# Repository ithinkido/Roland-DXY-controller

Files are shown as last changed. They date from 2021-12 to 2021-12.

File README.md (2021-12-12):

# Roland-DXY-controller
 A modern ESP32 based controller for Roland DXY plotter with i2c shift regisers for button mapping, OLED dispay, solenoid drivers and on board TMC 2208 silent stepper drivers. This Design uses standard STEP/DIR controll only.
 This is a two board design with a main controller and a daughter board that handles the USB-C serial connection and SD card. This allows for perfect placement of the connectors and the use of the exsisting openins in the plotter case. 

The board is designed to be a a plug in replacemnt with NO modifications to the existing plotter hardware. 
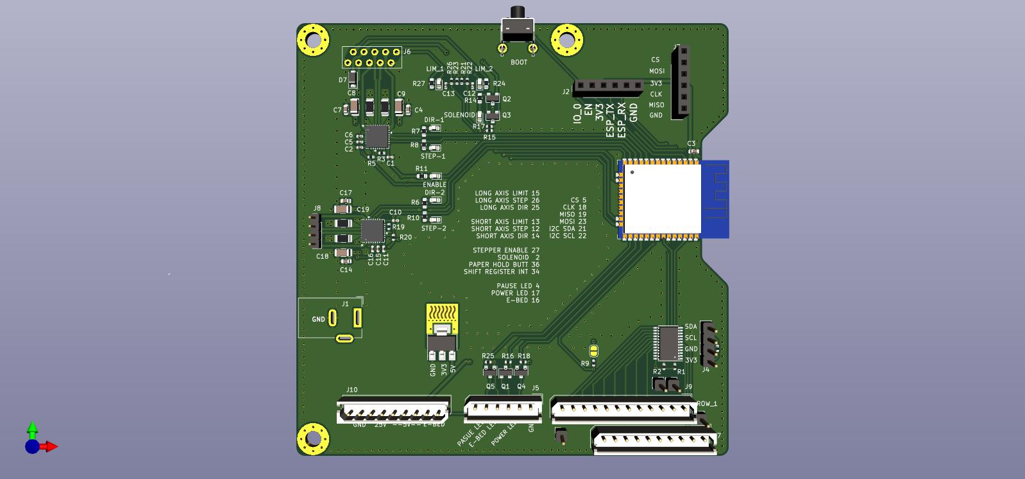
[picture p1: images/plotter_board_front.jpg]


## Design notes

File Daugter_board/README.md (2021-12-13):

This board takes care of the USB-C serial comms as well as the SD card. It is piggybacked onto the main board to postion the connectors correctly within the case openings.  

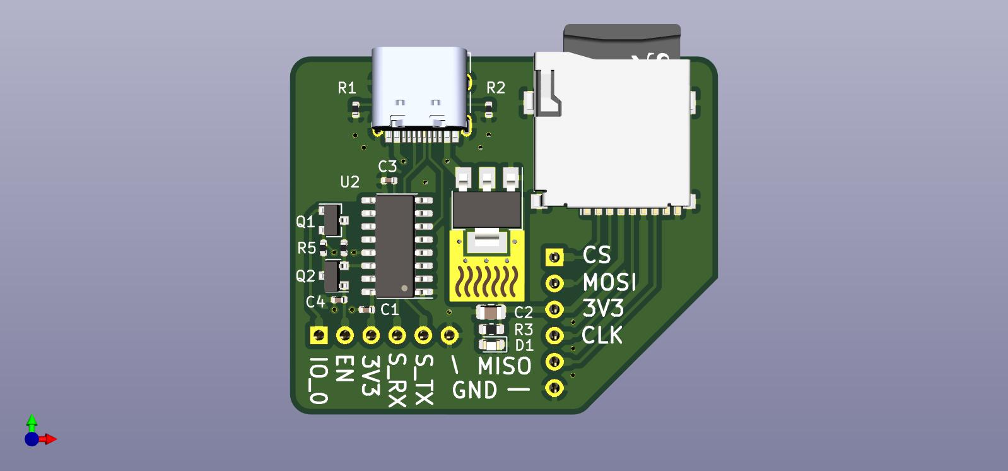
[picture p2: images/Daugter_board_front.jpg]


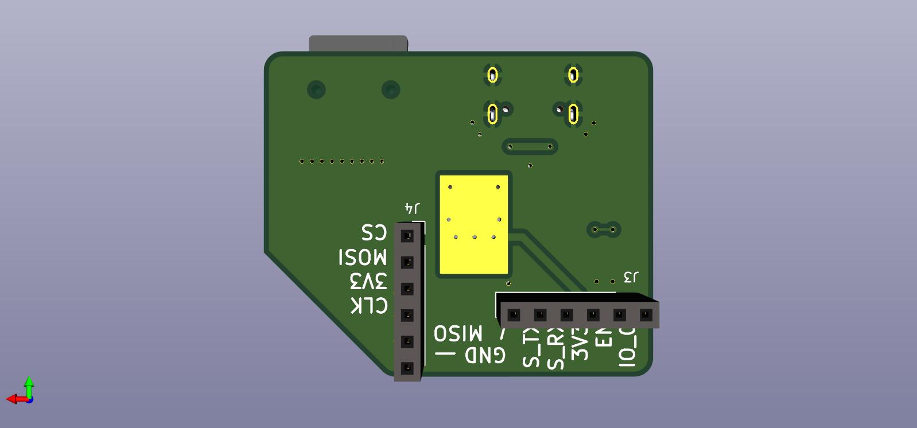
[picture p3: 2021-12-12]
images/Daugter_board_back.jpg

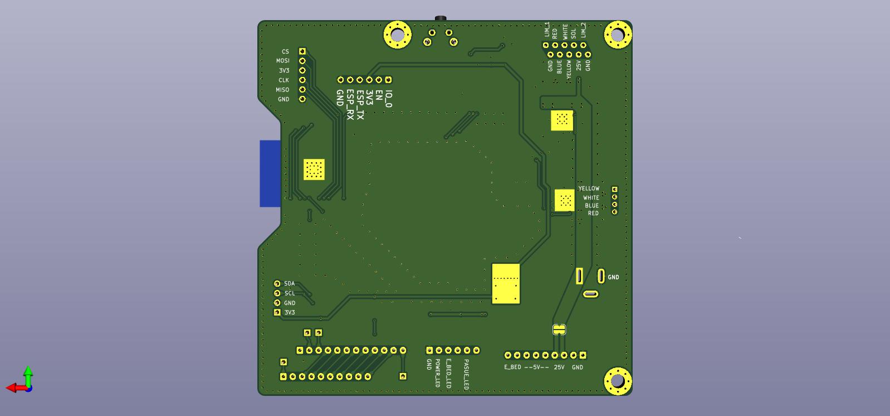
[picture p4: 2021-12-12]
images/plotter_board_back.jpg

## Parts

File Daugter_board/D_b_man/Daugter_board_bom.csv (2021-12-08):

Comment | Designator | Footprint | LCSC
10K | R5,R4 | Resistor_SMD:R_0402_1005Metric | C25744
MMBT3904 | Q1,Q2 | Package_TO_SOT_SMD:SOT-23 | C20526
USB_C_Receptacle_USB2.0 | J1 | Connector_USB:USB_C_Receptacle_HRO_TYPE-C-31-M-12 | C165948
5.1K | R2,R1 | Resistor_SMD:R_0402_1005Metric | C25905
100nf | C4 | Capacitor_SMD:C_0402_1005Metric | C1525
1uF | C1 | Capacitor_SMD:C_0402_1005Metric | C52923
Micro_SD_Card | J2 | plotter_board:Conn_uSDcard | C111196
1uF | C2 | Capacitor_SMD:C_0805_2012Metric | C28323
AP1117-33 | U1 | Package_TO_SOT_SMD:SOT-223-3_TabPin2 | C6186
USB_Serial | J3 | Connector_PinSocket_2.54mm:PinSocket_1x06_P2.54mm_Vertical
SD_Card | J4 | Connector_PinSocket_2.54mm:PinSocket_1x06_P2.54mm_Vertical
100nF | C3 | Capacitor_SMD:C_0402_1005Metric | C1525
2K2 | R3 | Resistor_SMD:R_0603_1608Metric | C4190
CH340B | U2 | Package_SO:SOIC-16_3.9x9.9mm_P1.27mm | C81010
LED | D1 | LED_SMD:LED_0603_1608Metric | C72041

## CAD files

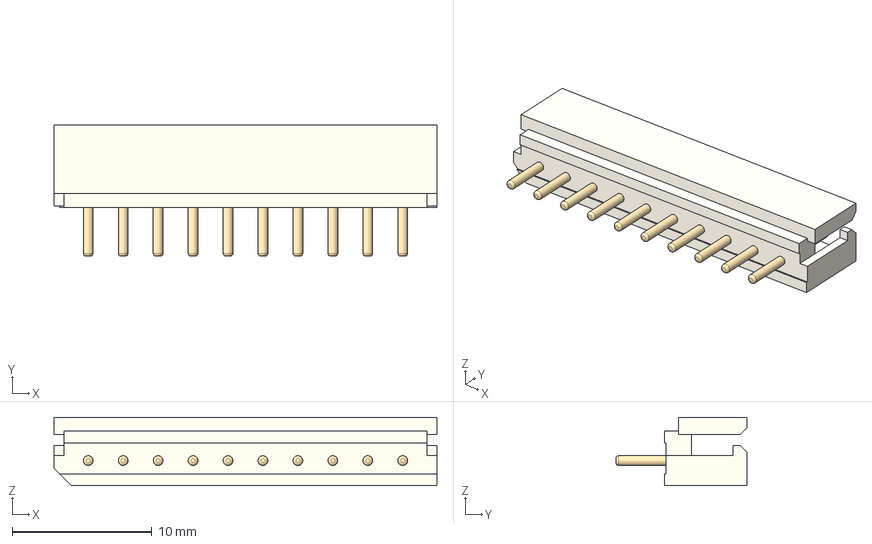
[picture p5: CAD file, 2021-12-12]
3D/Mini_Spox_10pin v2.step
27.4 x 9.40 x 4.90 mm

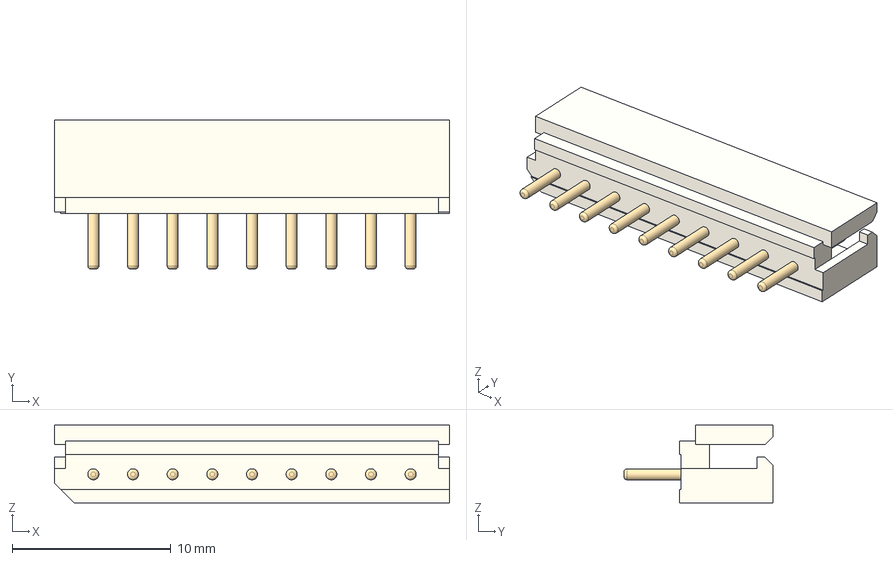
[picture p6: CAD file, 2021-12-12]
3D/Mini_Spox_9pin v2.step
24.9 x 9.40 x 4.90 mm

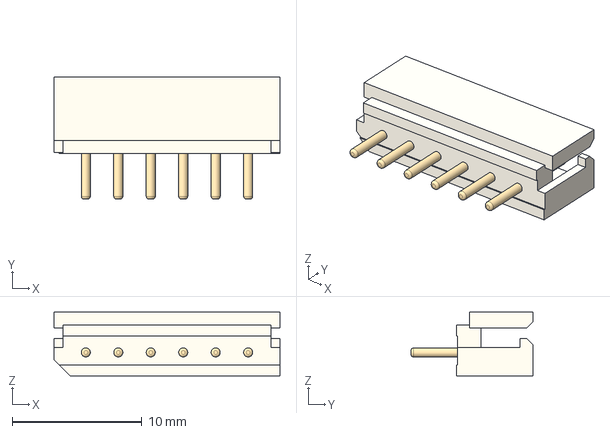
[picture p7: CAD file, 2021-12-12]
3D/Mini_Spox_6pin v3.step
17.4 x 9.40 x 4.90 mm

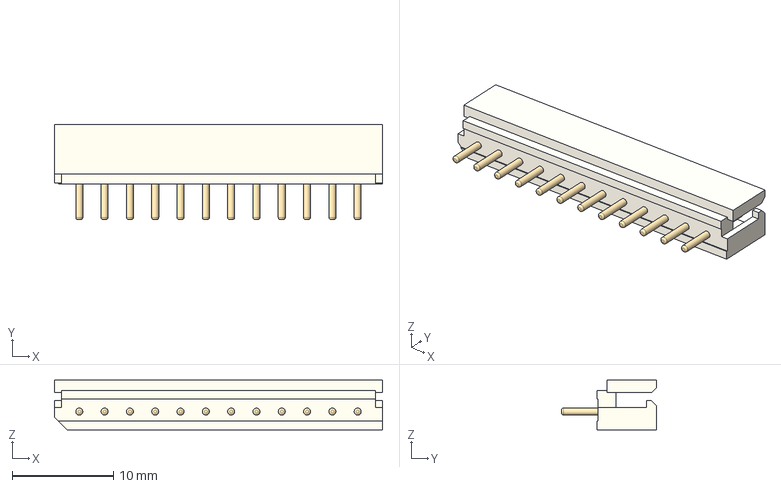
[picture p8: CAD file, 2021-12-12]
3D/Mini_Spox_12pin v2.step
32.4 x 9.40 x 4.90 mm

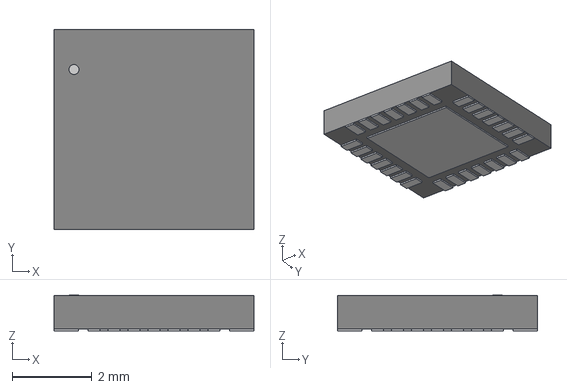
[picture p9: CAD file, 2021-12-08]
3D/QFN28_5X5_TRI.step
5.00 x 5.00 x 0.892 mm

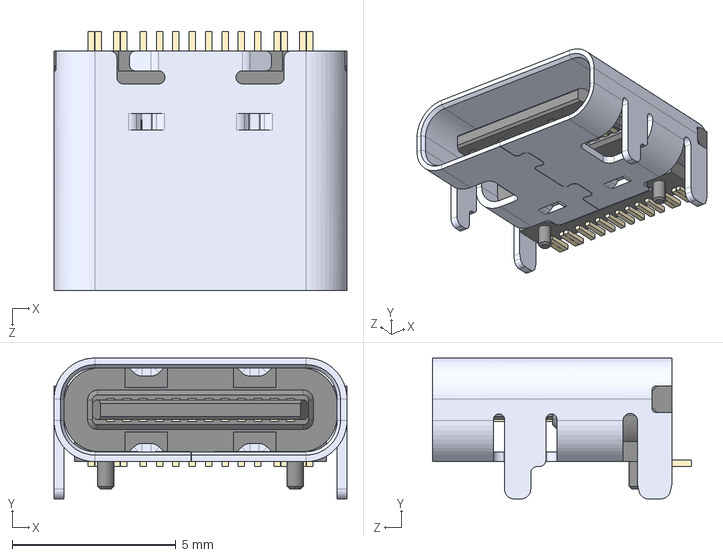
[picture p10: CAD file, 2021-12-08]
3D/TYPE-C-31-M-12--3DModel-STEP-56544.step
8.94 x 4.30 x 7.90 mm

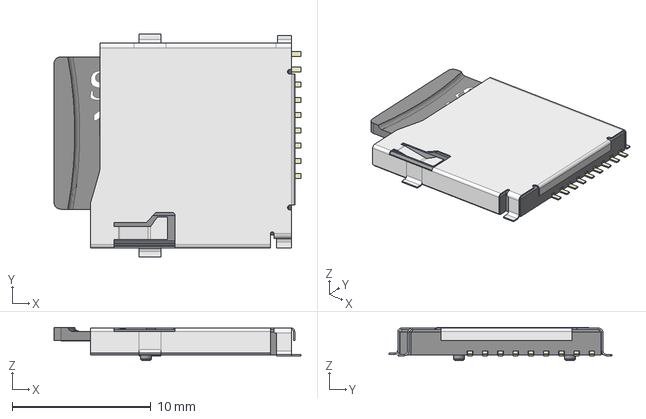
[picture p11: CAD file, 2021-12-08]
3D/TF-15x15_SD_Card.step
17.8 x 16.1 x 2.40 mm

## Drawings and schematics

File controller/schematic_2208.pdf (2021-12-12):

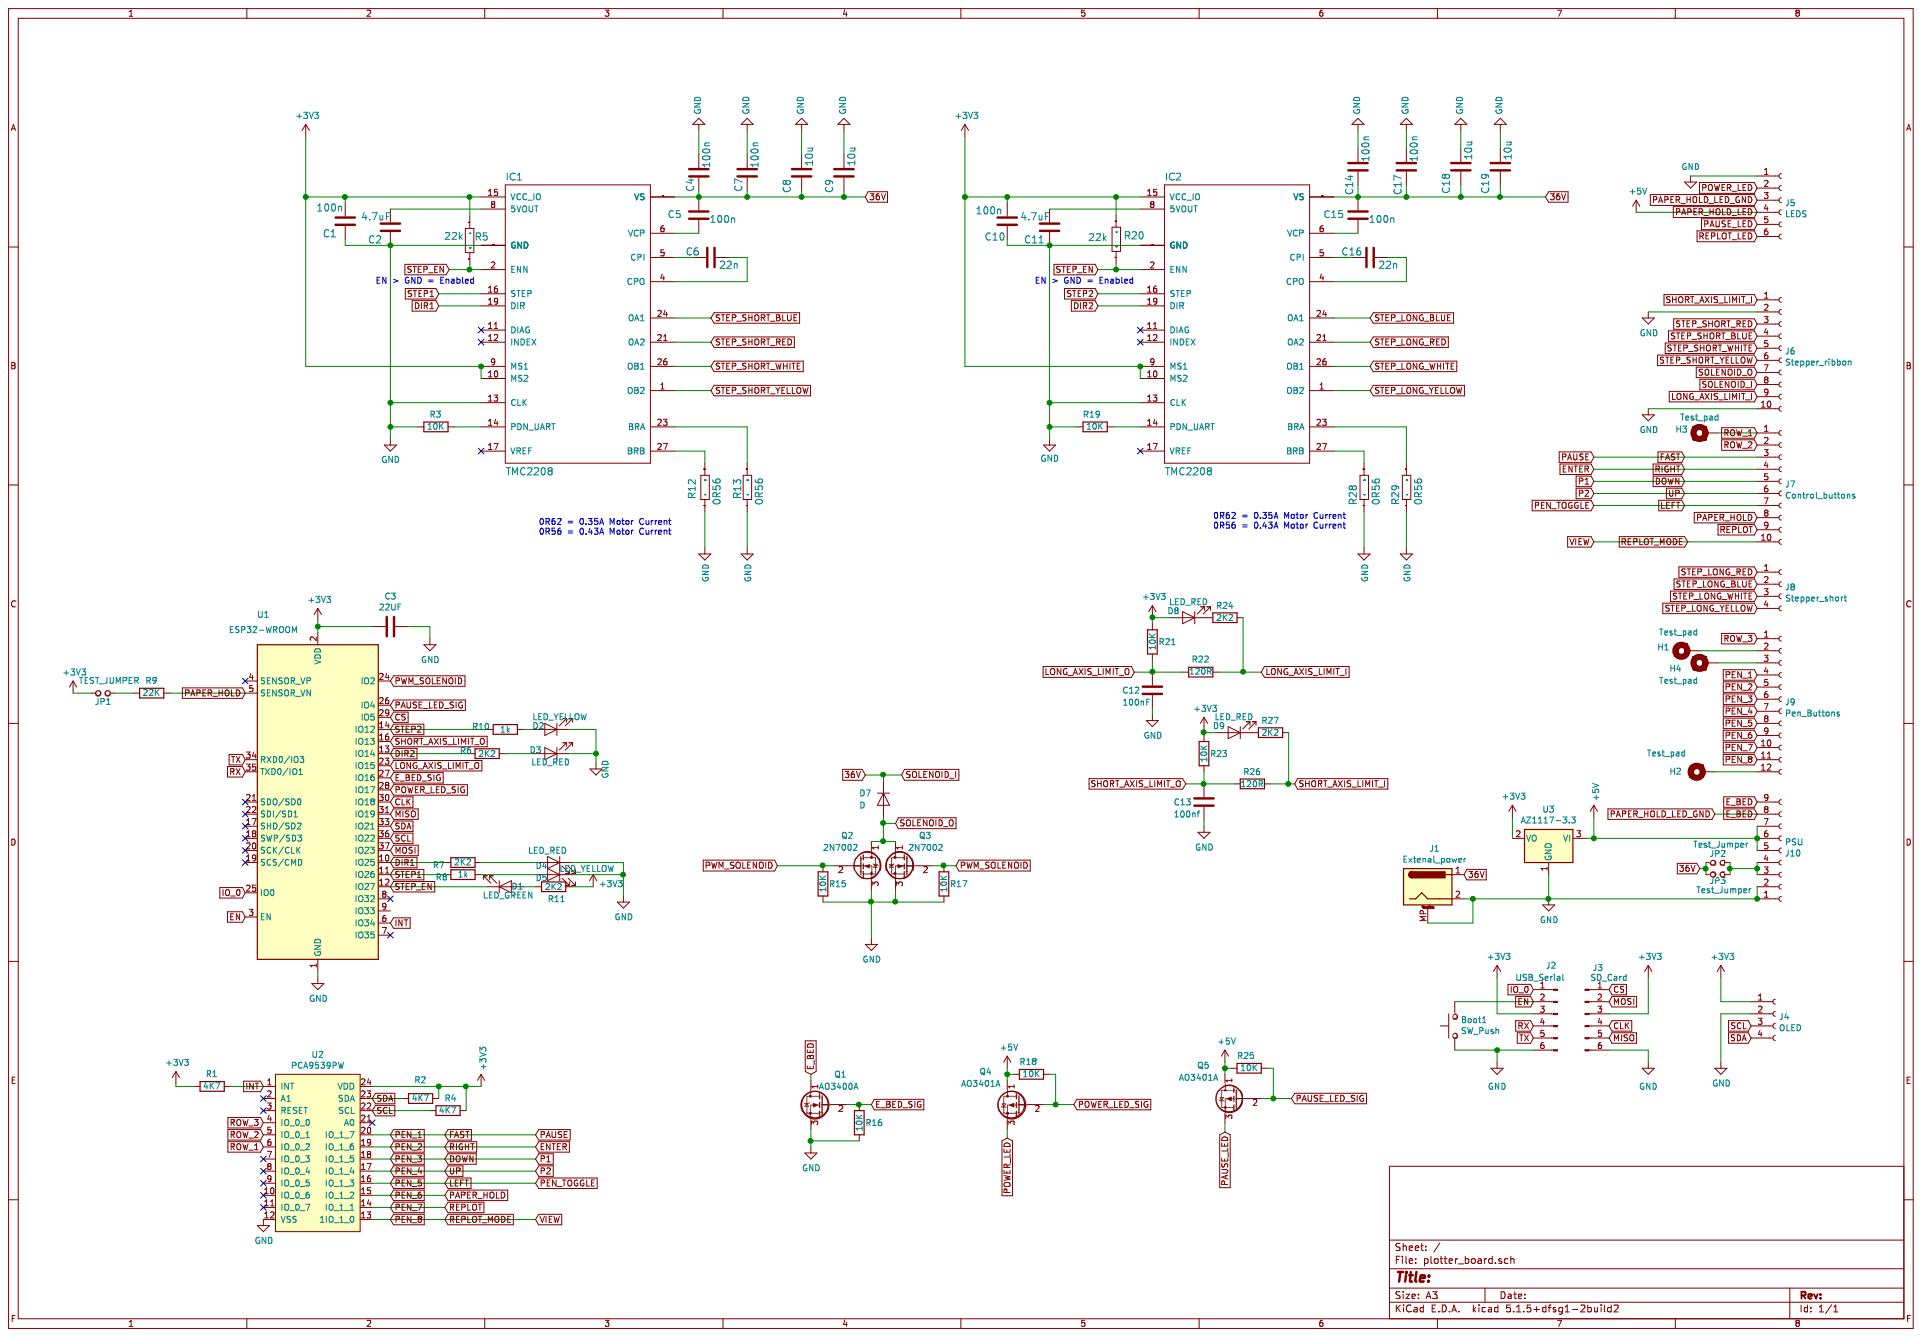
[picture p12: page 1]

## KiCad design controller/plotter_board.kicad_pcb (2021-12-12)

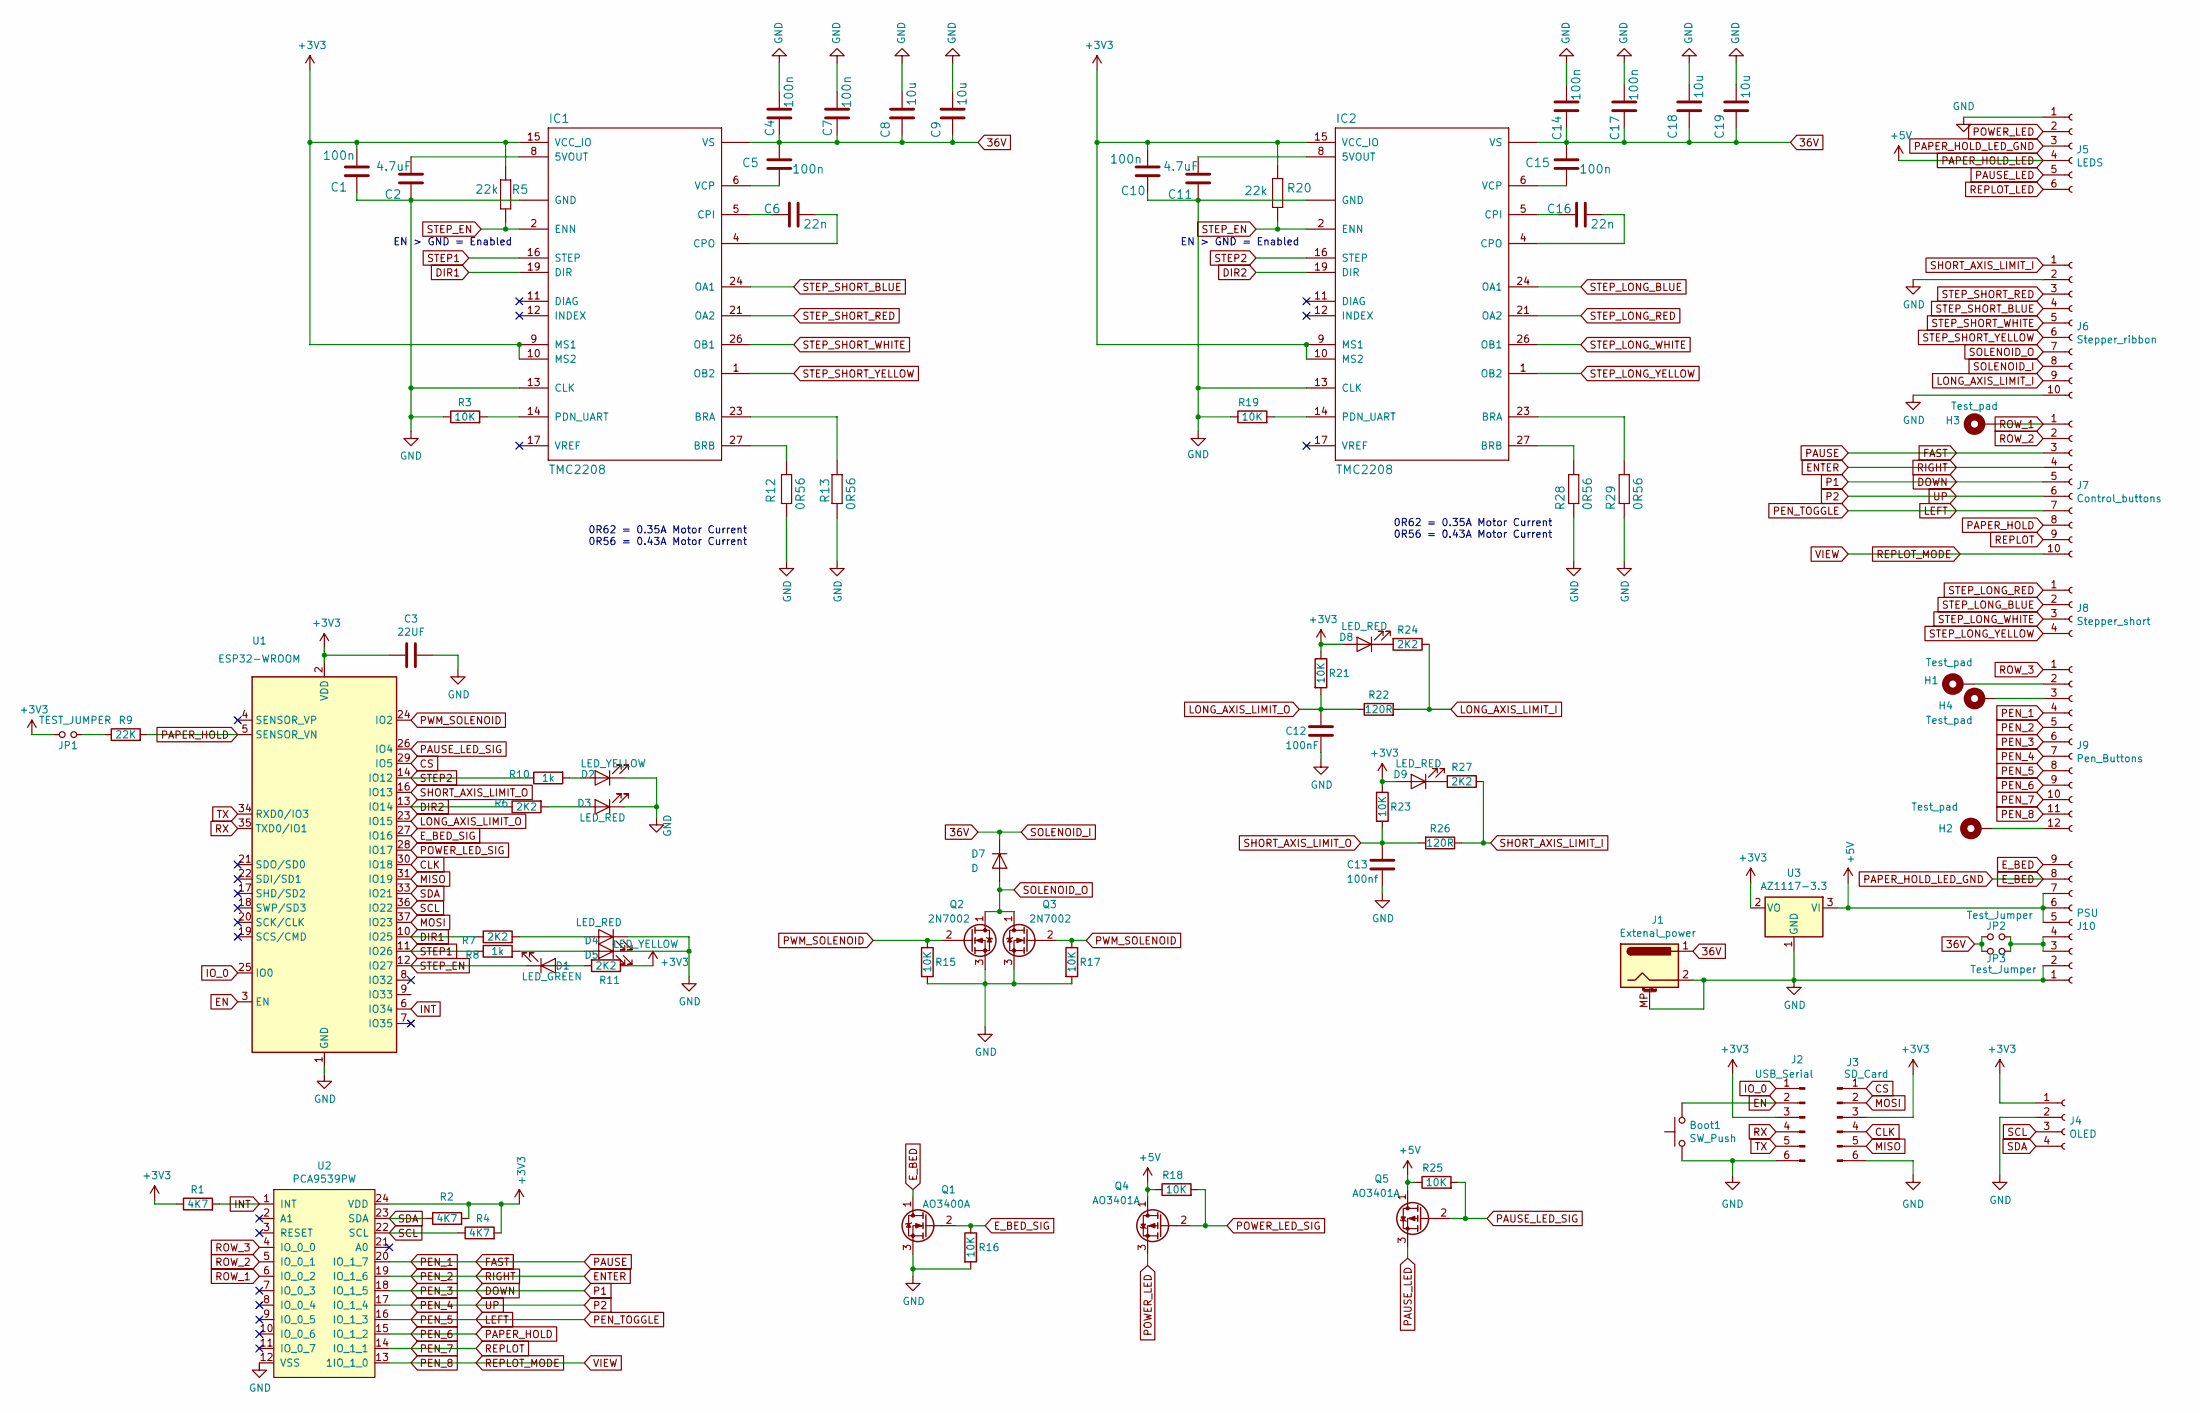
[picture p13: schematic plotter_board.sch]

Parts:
Boot1: SW_Push; SW_Tactile_SPST_Angled_PTS645Vx58-2LFS
C1, C5, C10, C15: 100n; C_0402_1005Metric; LCSC C1525
C2, C11: 4.7uF; C_0402_1005Metric; LCSC C23733
C3: 22UF; C_0603_1608Metric; LCSC C59461
C4, C7, C14, C17: 100n; C_0603_1608Metric; LCSC C14663
C6, C16: 22n; C_0402_1005Metric; LCSC C1532
C8, C9, C18, C19: 10u; C_1206_3216Metric; LCSC C13585
C12: 100nF; C_0402_1005Metric; LCSC C1525
C13: 100nf; C_0402_1005Metric; LCSC C1525
D1: LED_GREEN; LED_0603_1608Metric; LCSC C72043
D2, D5: LED_YELLOW; LED_0603_1608Metric; LCSC C72038
D3, D4, D8, D9: LED_RED; LED_0603_1608Metric; LCSC C2286
D7: D; D_SOD-123F; LCSC C64898
H1, H2, H3, H4: Test_pad; PinHeader_1x01_P2.54mm_Vertical
IC1, IC2: TMC2208; TMC2209-LA; LCSC C465949
J1: Extenal_power; BarrelJack_Wuerth_6941xx301002
J2: USB_Serial; PinSocket_1x06_P2.54mm_Vertical
J3: SD_Card; PinSocket_1x06_P2.54mm_Vertical
J4: OLED; PinHeader_1x04_P2.54mm_Vertical
J5: LEDS; Molex_SPOX_5267-06A_1x06_P2.50mm_Vertical
J6: Stepper_ribbon; Ribbon_1.25mm_FFC_10pin
J7: Control_buttons; Molex_SPOX_5267-10A_1x10_P2.50mm_Vertical
J8: Stepper_short; PinHeader_1x04_P2.00mm_Vertical
J9: Pen_Buttons; Molex_SPOX_5267-12A_1x12_P2.50mm_Vertical
J10: PSU; Molex_SPOX_5267-09A_1x09_P2.50mm_Vertical
JP1: TEST_JUMPER; SolderJumper-2_P1.3mm_Open_RoundedPad1.0x1.5mm
JP2, JP3: Test_Jumper; SolderJumper-2_P1.3mm_Open_RoundedPad1.0x1.5mm
Q1: AO3400A; SOT-23; LCSC C20917
Q2, Q3: 2N7002; SOT-23; LCSC C8545
Q4, Q5: AO3401A; SOT-23; LCSC C15127
R1: 4K7; R_0402_1005Metric; LCSC C25744
R2, R4: 4K7; R_0402_1005Metric; LCSC C25900
R3, R15, R16, R17, R18, R19, R21, R23, R25: 10K; R_0402_1005Metric; LCSC C25744
R5, R20: 22k; R_0402_1005Metric; LCSC C25768
R6, R7, R11, R24, R27: 2K2; R_0603_1608Metric; LCSC C4190
R8, R10: 1k; R_0603_1608Metric; LCSC C21190
R9: 22K; R_0402_1005Metric; LCSC C25768
R12, R13, R28, R29: 0R56; R_1206_3216Metric; LCSC C104949
R22, R26: 120R; R_0402_1005Metric; LCSC C25079
U1: ESP32-WROOM; ESP32-WROOM-32; LCSC C473012
U2: PCA9539PW; TSSOP-24_4.4x7.8mm_P0.65mm; LCSC C129516
U3: AZ1117-3.3; SOT-223-3_TabPin2

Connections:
36V: C4.1, C5.1, C7.1, C8.1, C9.1, C14.1, C15.1, C17.1, C18.1, C19.1, D7.1 (K), IC1.22 (VS), IC1.28 (VS), IC2.22 (VS), IC2.28 (VS), J1.1, J6.8, JP2.1, JP3.1
+3V3: C1.2, C3.2, C10.2, D8.2 (A), D9.2 (A), IC1.9 (MS1), IC1.10 (MS2), IC1.15 (VCC_IO), IC2.9 (MS1), IC2.10 (MS2), IC2.15 (VCC_IO), J2.3, J3.3, J4.1, JP1.2, R1.1, R2.2, R4.2, R5.1, R11.1, R20.1, R21.1, R23.1, U1.2 (VDD), U2.24 (VDD), U3.2 (VO)
CLK: J3.4, U1.30 (IO18)
CS: J3.1, U1.29 (IO5)
DIR1: IC1.19 (DIR), R7.1, U1.10 (IO25)
DIR2: IC2.19 (DIR), R6.1, U1.13 (IO14)
DOWN: J7.5, J9.6, U2.18 (IO_1_5)
EN: Boot1.2, J2.2, U1.3 (EN)
ENTER: J7.4, J9.5, U2.19 (IO_1_6)
E_BED: J5.3, J10.8, J10.9, Q1.1 (D)
E_BED_SIG: Q1.2 (G), R16.1, U1.27 (IO16)
FAST: J7.3, J9.4, U2.20 (IO_1_7)
GND: Boot1.1, C1.1, C2.1, C3.1, C4.2, C7.2, C8.2, C9.2, C10.1, C11.1, C12.2, C13.2, C14.2, C17.2, C18.2, C19.2, D2.1 (K), D3.1 (K), D4.1 (K), D5.1 (K), IC1.3 (GND), IC1.13 (CLK), IC1.18 (GND), IC1.29, IC1.TP (GND), IC2.3 (GND), IC2.13 (CLK), IC2.18 (GND), IC2.TP (GND), J1.2, J1.MP (MountPin), J2.6, J3.6, J4.2, J5.1, J6.2, J6.10, J10.1, J10.2, Q1.3 (S), Q2.3 (S), Q3.3 (S), R3.1, R12.1, R13.1, R15.2, R16.2, R17.2, R19.1, R28.1, R29.1, U1.1 (GND), U1.15 (GND), U1.38 (GND), U1.39 (GND), U2.12 (VSS), U3.1 (GND); also elsewhere on the board
INT: R1.2, U1.6 (IO34), U2.1 (INT)
IO_0: J2.1, U1.25 (IO0)
LEFT: J7.7, J9.8, U2.16 (IO_1_3)
LONG_AXIS_LIMIT_I: J6.9, R22.2, R24.1
LONG_AXIS_LIMIT_O: C12.1, R21.2, R22.1, U1.23 (IO15)
MISO: J3.5, U1.31 (IO19)
MOSI: J3.2, U1.37 (IO23)
unnamed: C2.2, IC1.8 (5VOUT)
unnamed: C5.2, IC1.6 (VCP)
unnamed: C6.1, IC1.5 (CPI)
unnamed: C6.2, IC1.4 (CPO)
unnamed: C11.2, IC2.8 (5VOUT)
unnamed: C15.2, IC2.6 (VCP)
unnamed: C16.1, IC2.5 (CPI)
unnamed: C16.2, IC2.4 (CPO)
unnamed: D1.2 (A), R11.2
unnamed: D2.2 (A), R10.2
unnamed: D3.2 (A), R6.2
unnamed: D4.2 (A), R7.2
unnamed: D5.2 (A), R8.2
unnamed: D8.1 (K), R24.2
unnamed: D9.1 (K), R27.2
unnamed: H1.1, J9.2
unnamed: H2.1, J9.12
unnamed: H4.1, J9.3
unnamed: IC1.14 (PDN_UART), R3.2
unnamed: IC1.23 (BRA), R13.2
unnamed: IC1.27 (BRB), R12.2
unnamed: IC2.14 (PDN_UART), R19.2
unnamed: IC2.23 (BRA), R29.2
unnamed: IC2.27 (BRB), R28.2
unnamed: J10.3, J10.4, JP2.2, JP3.2
unnamed: JP1.1, R9.1
P2: J7.6, J9.7, U2.17 (IO_1_4)
PAPER_HOLD: J7.8, J9.9, R9.2, U1.5 (SENSOR_VN), U2.15 (IO_1_2)
PAPER_HOLD_LED: J5.4, J10.5, J10.6, J10.7, Q4.1 (D), Q5.1 (D), R18.1, R25.1, U3.3 (VI)
PAUSE_LED: J5.5, Q5.3 (S)
PAUSE_LED_SIG: Q5.2 (G), R25.2, U1.26 (IO4)
PEN_7: J7.9, J9.10, U2.14 (IO_1_1)
PEN_8: J7.10, J9.11, U2.13 (1IO_1_0)
POWER_LED: J5.2, Q4.3 (S)
POWER_LED_SIG: Q4.2 (G), R18.2, U1.28 (IO17)
PWM_SOLENOID: Q2.2 (G), Q3.2 (G), R15.1, R17.1, U1.24 (IO2); also elsewhere on the board
REPLOT_LED: J5.6
ROW_1: H3.1, J7.1, U2.6 (IO_0_2)
ROW_2: J7.2, U2.5 (IO_0_1)
ROW_3: J9.1, U2.4 (IO_0_0)
RX: J2.4, U1.35 (TXD0/IO1)
SCL: J4.3, R4.1, U1.36 (IO22), U2.22 (SCL)
SDA: J4.4, R2.1, U1.33 (IO21), U2.23 (SDA)
SHORT_AXIS_LIMIT_I: J6.1, R26.1, R27.1
SHORT_AXIS_LIMIT_O: C13.1, R23.2, R26.2, U1.16 (IO13)
SOLENOID_O: D7.2 (A), J6.7, Q2.1 (D), Q3.1 (D)
STEP1: IC1.16 (STEP), R8.1, U1.11 (IO26)
STEP2: IC2.16 (STEP), R10.1, U1.14 (IO12)
STEP_EN: D1.1 (K), IC1.2 (ENN), IC2.2 (ENN), R5.2, R20.2, U1.12 (IO27)
STEP_LONG_BLUE: IC2.24 (OA1), J8.2
STEP_LONG_RED: IC2.21 (OA2), J8.1
STEP_LONG_WHITE: IC2.26 (OB1), J8.3
STEP_LONG_YELLOW: IC2.1 (OB2), J8.4
STEP_SHORT_BLUE: IC1.24 (OA1), J6.4
STEP_SHORT_RED: IC1.21 (OA2), J6.3
STEP_SHORT_WHITE: IC1.26 (OB1), J6.5
STEP_SHORT_YELLOW: IC1.1 (OB2), J6.6
TX: J2.5, U1.34 (RXD0/IO3)

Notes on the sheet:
EN > GND = Enabled
0R62 = 0.35A Motor Current 0R56 = 0.43A Motor Current

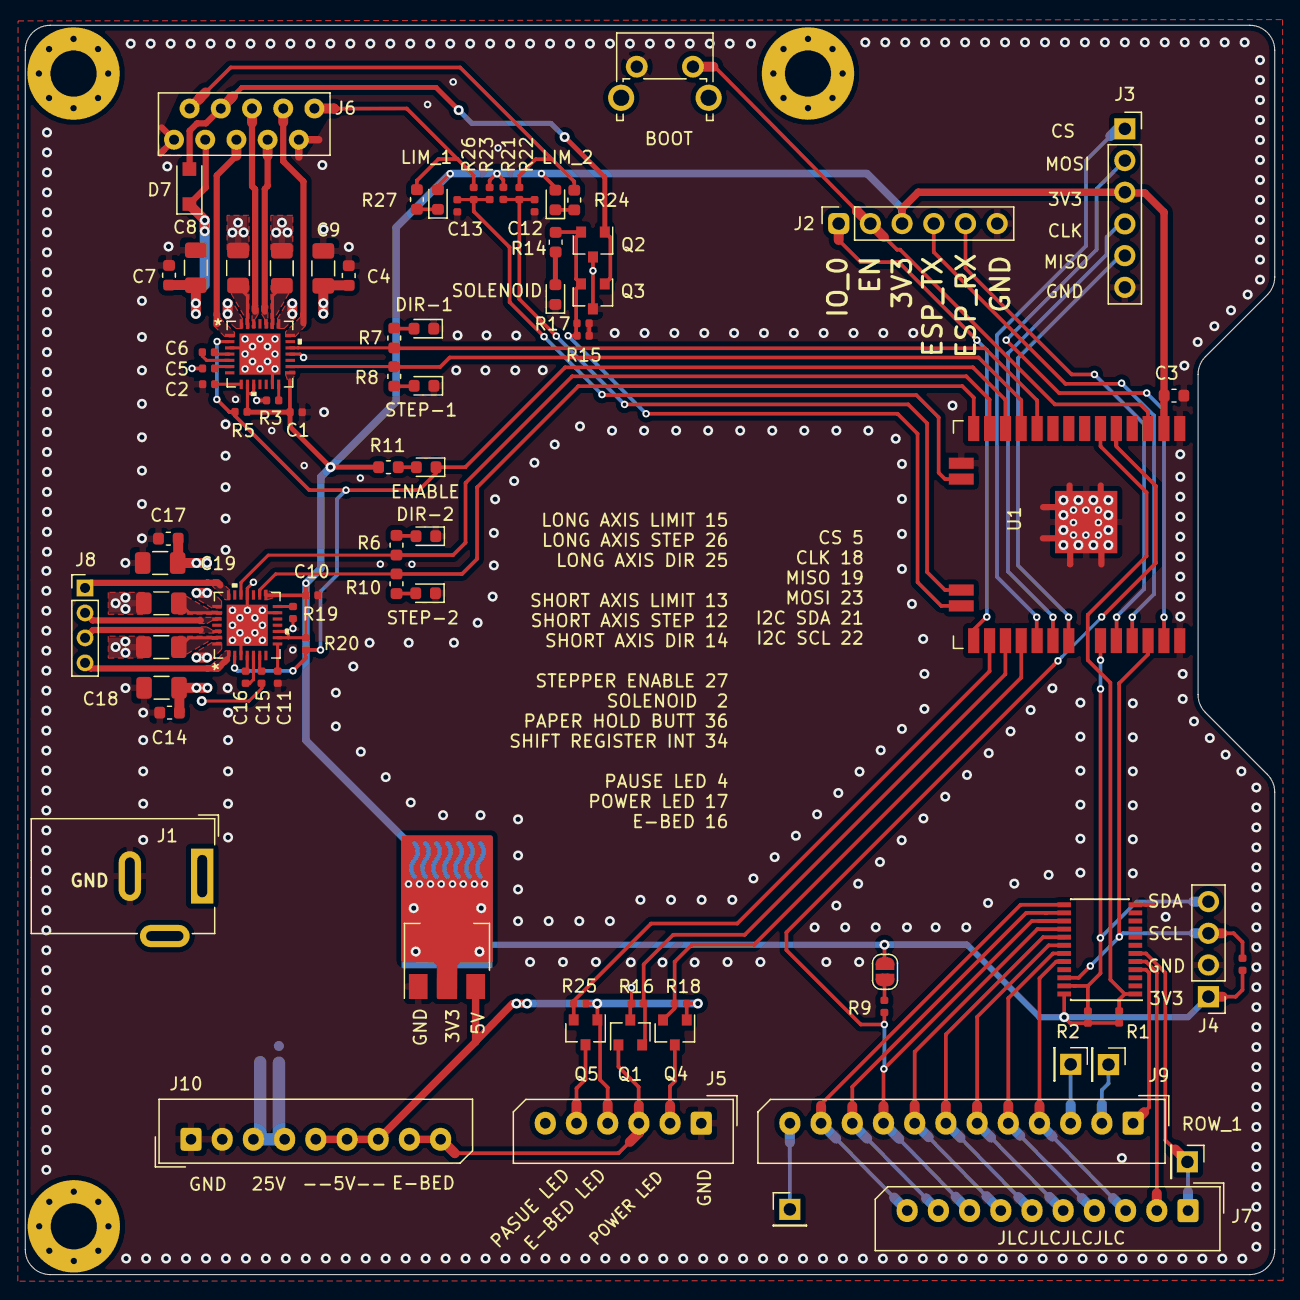
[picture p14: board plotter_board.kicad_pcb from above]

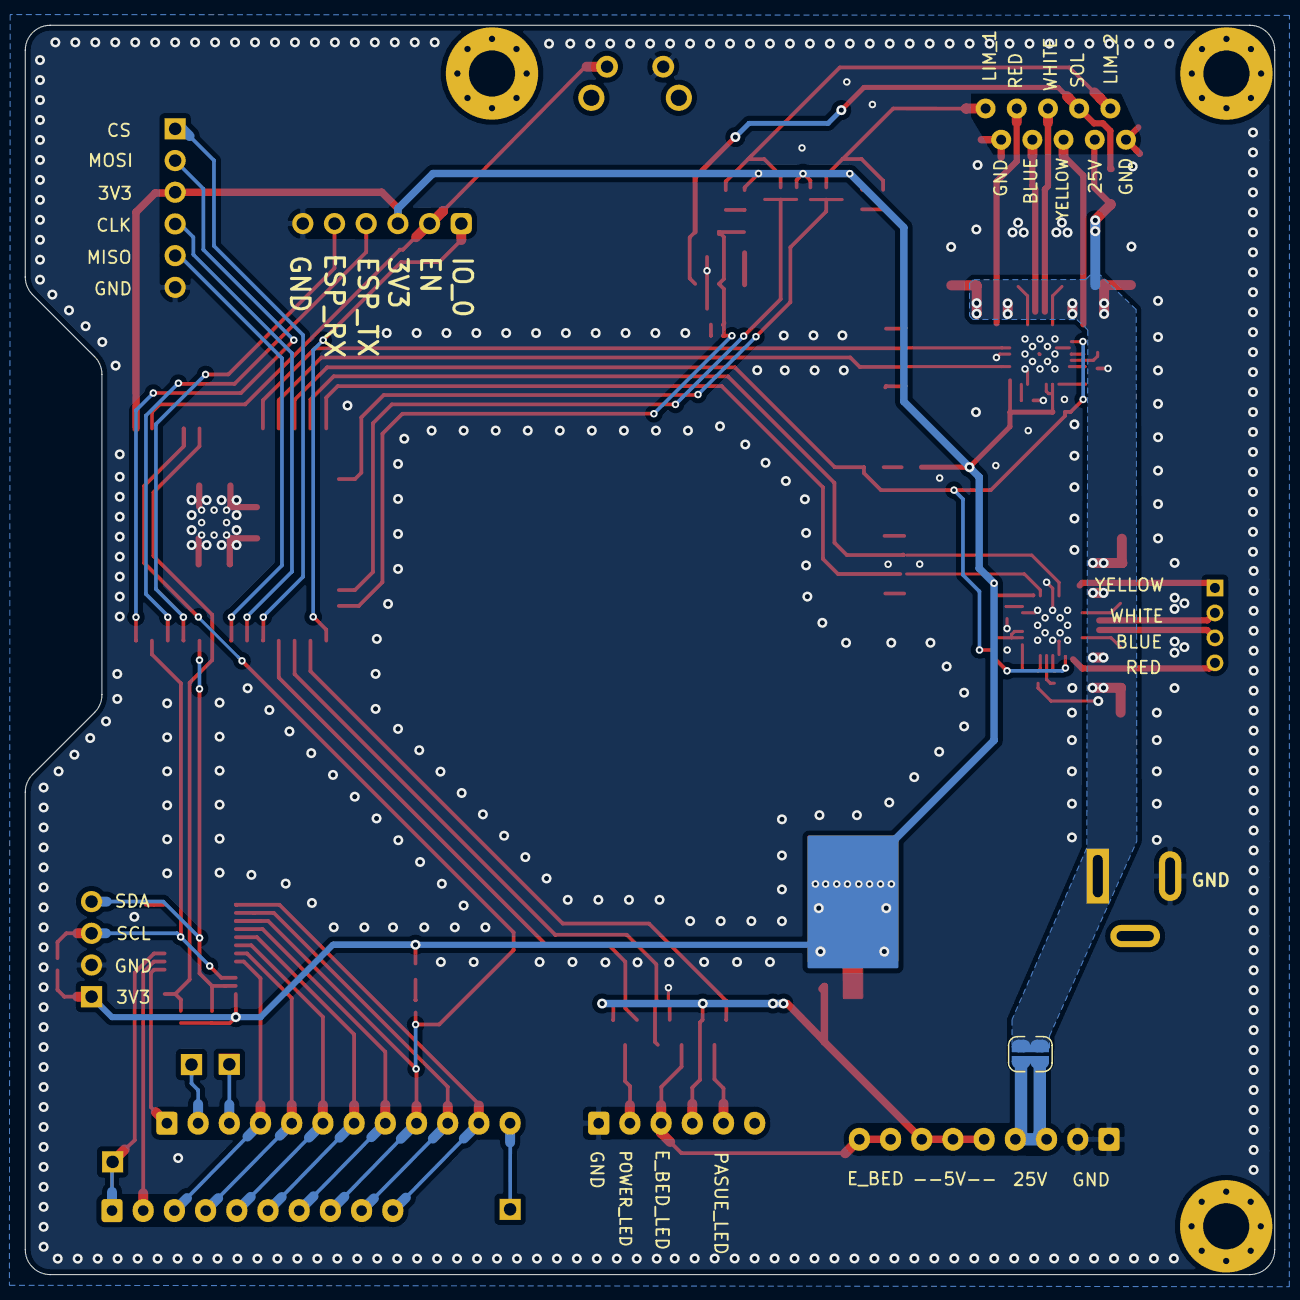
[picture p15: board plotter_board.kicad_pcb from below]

Board: 2 copper layers, 100.1 x 100.1 mm, 86 parts (3 on the bottom side), 78 nets.

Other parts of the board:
D6: LED_BLUE; LED_0603_1608Metric
R14: 2K2; R_0603_1608Metric
svg2mod: G***; pad_all

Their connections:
GND: D6.1; also elsewhere on the board
unnamed: D6.2, R14.1
PWM_SOLENOID: R14.2; also elsewhere on the board

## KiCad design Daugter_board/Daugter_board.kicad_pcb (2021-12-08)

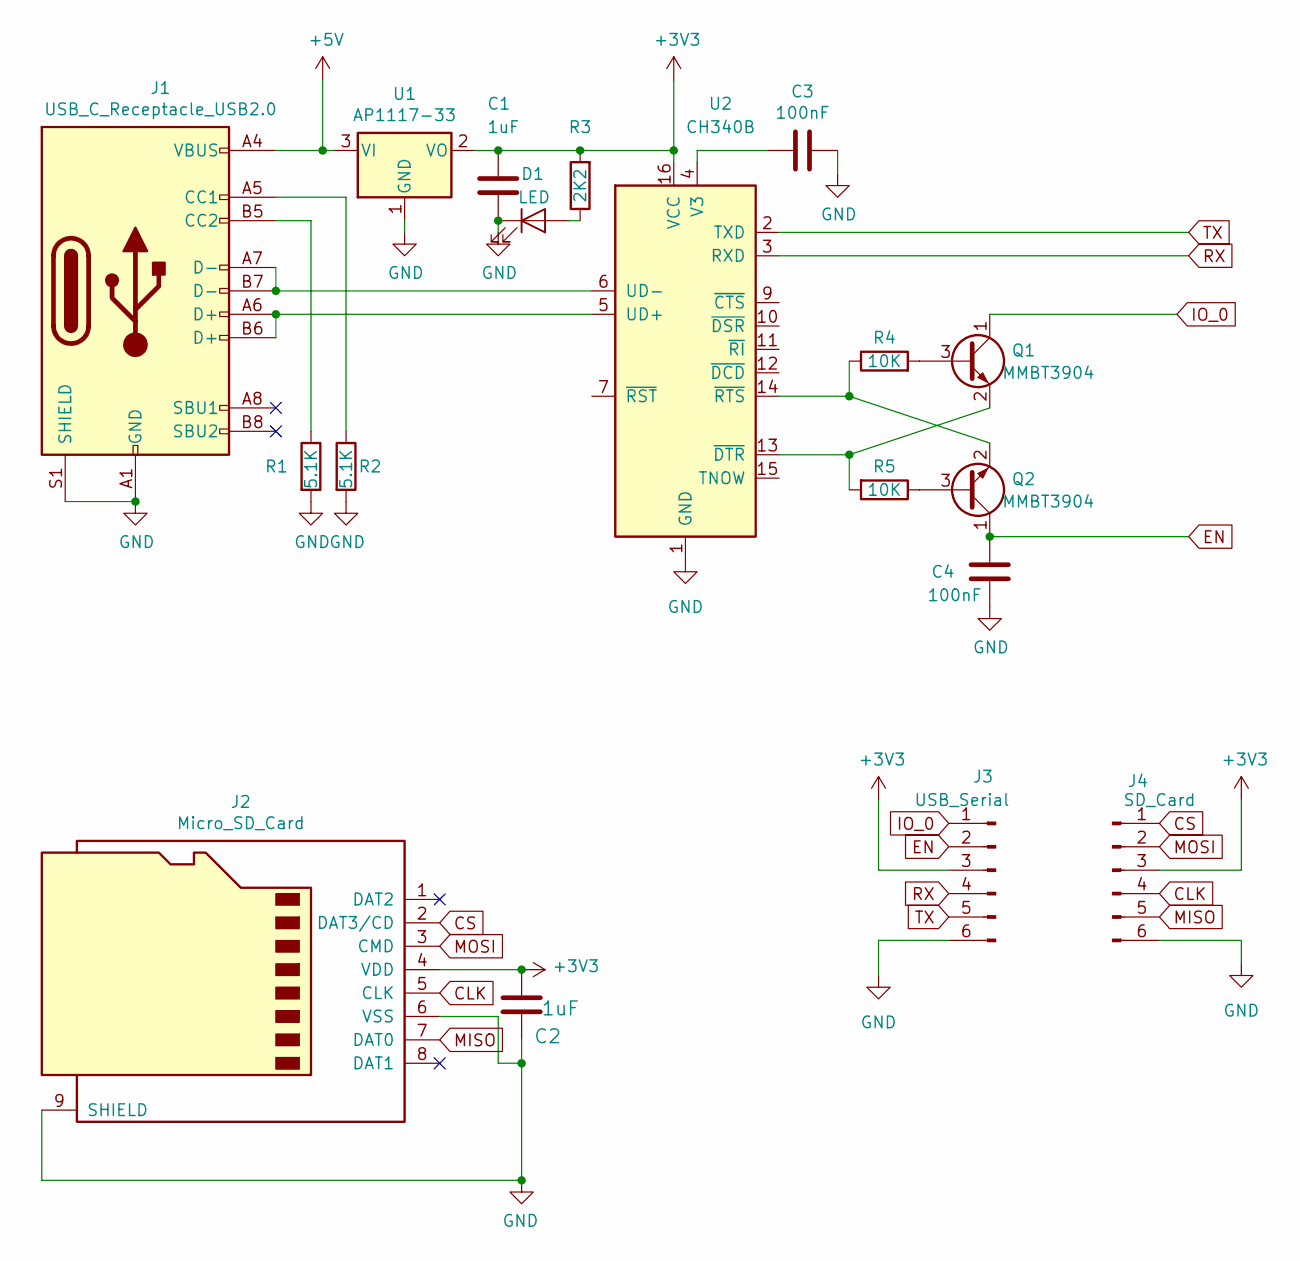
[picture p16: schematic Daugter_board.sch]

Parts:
C1: 1uF; C_0402_1005Metric; LCSC C52923
C2: 1uF; C_0805_2012Metric; LCSC C28323
C3, C4: 100nF; C_0402_1005Metric; LCSC C1525
D1: LED; LED_0603_1608Metric; LCSC C72041
J1: USB_C_Receptacle_USB2.0; USB_C_Receptacle_HRO_TYPE-C-31-M-12; LCSC C165948
J2: Micro_SD_Card; Conn_uSDcard; LCSC C111196
J3: USB_Serial; PinSocket_1x06_P2.54mm_Vertical
J4: SD_Card; PinSocket_1x06_P2.54mm_Vertical
Q1, Q2: MMBT3904; SOT-23; LCSC C20526
R1, R2: 5.1K; R_0402_1005Metric; LCSC C25905
R3: 2K2; R_0603_1608Metric; LCSC C4190
R4, R5: 10K; R_0402_1005Metric; LCSC C25744
U1: AP1117-33; SOT-223-3_TabPin2; LCSC C6186
U2: CH340B; SOIC-16_3.9x9.9mm_P1.27mm; LCSC C81010

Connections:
+3V3: C1.1, C2.2, J2.4 (VDD), J3.3, J4.3, R3.2, U1.2 (VO), U2.16 (VCC)
+5V: J1.A4 (VBUS), J1.A9 (VBUS), J1.B4 (VBUS), J1.B9 (VBUS), U1.3 (VI)
CLK: J2.5 (CLK), J4.4
CS: J2.2 (DAT3/CD), J4.1
EN: C4.2, J3.2, Q2.1 (C)
GND: C1.2, C2.1, C3.1, C4.1, D1.1 (K), J1.A1 (GND), J1.A12 (GND), J1.B1 (GND), J1.B12 (GND), J1.S1 (SHIELD), J2.6 (VSS), J2.9 (SHIELD), J3.6, J4.6, R1.2, R2.2, U1.1 (GND), U2.1 (GND)
IO_0: J3.1, Q1.1 (C)
MISO: J2.7 (DAT0), J4.5
MOSI: J2.3 (CMD), J4.2
unnamed: C3.2, U2.4 (V3)
unnamed: D1.2 (A), R3.1
unnamed: J1.A5 (CC1), R2.1
unnamed: J1.A6 (D+), J1.B6 (D+), U2.5 (UD+)
unnamed: J1.A7 (D-), J1.B7 (D-), U2.6 (UD-)
unnamed: J1.B5 (CC2), R1.1
unnamed: Q1.2 (E), R5.2, U2.13 (~DTR)
unnamed: Q1.3 (B), R4.2
unnamed: Q2.2 (E), R4.1, U2.14 (~RTS)
unnamed: Q2.3 (B), R5.1
RX: J3.4, U2.3 (RXD)
TX: J3.5, U2.2 (TXD)

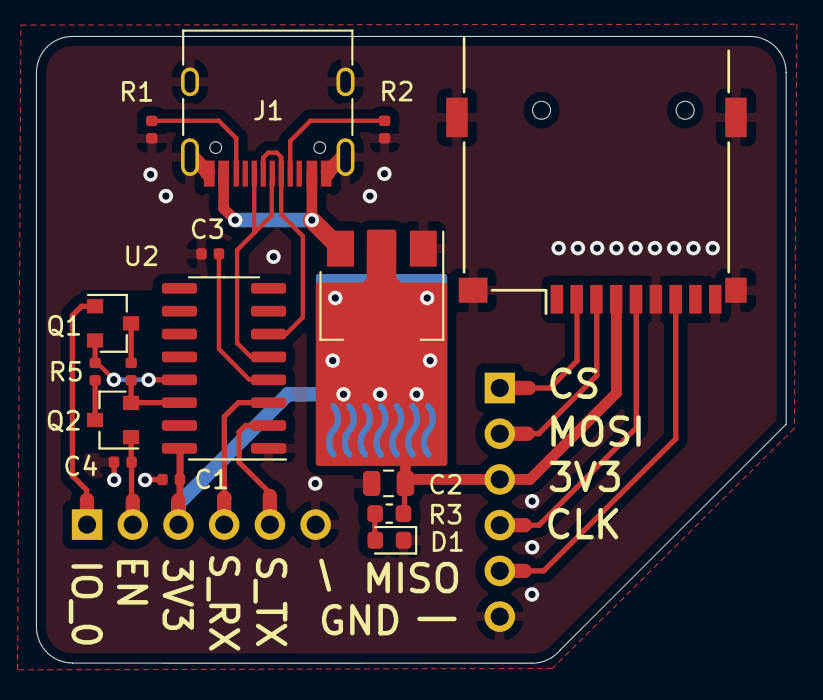
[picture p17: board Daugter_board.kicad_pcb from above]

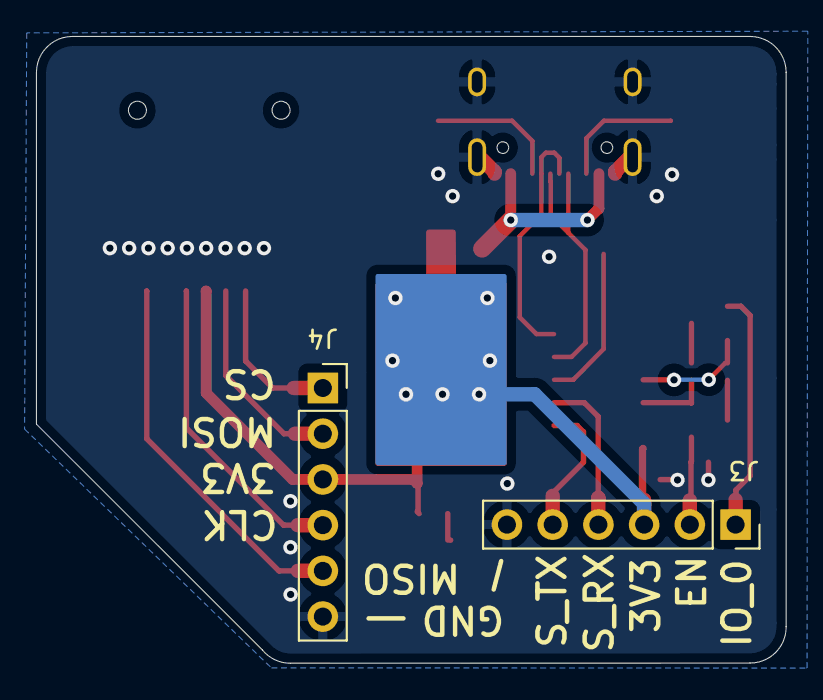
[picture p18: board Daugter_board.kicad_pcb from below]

Board: 2 copper layers, 41.7 x 34.8 mm, 19 parts (3 on the bottom side), 21 nets.

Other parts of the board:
svg2mod: G***; pad_all

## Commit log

2021-12-08 Fix pin maps
    [plotter_board.kicad_pcb, plotter_board.sch]
2021-12-13 Add info to Daughter board
